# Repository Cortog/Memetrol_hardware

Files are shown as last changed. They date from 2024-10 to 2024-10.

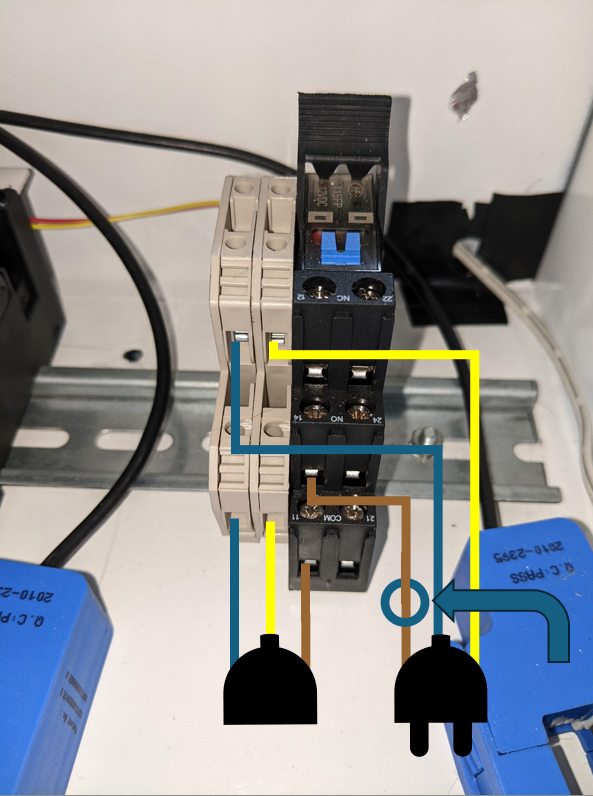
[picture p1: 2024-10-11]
relays_connection_diagram.png

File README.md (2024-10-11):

## Context
This repository contains the hardware design files for the Memetrol project. This project can control three washing machines and one dryer. Users can authenticate themselves using an RFID badge. The system logs the usage of the machines. A webserver on the system serves these logs to the administrator.

## Hardware
The hardware consists of a Raspberry Pi zero W and a Waveshare RP2040-zero both mounted on the base PCB. This PCB also contains the power supply, the relay drivers and analog circuitry for the current sensors. The Raspberry Pi is connected to the Waveshare RP2040-zero with UART. The Waveshare RP2040-zero is connected to the relay drivers and the current measurement circuitry. The Raspberry Pi is connected to the rest of the peripherals using a 20 pin ribbon cable. This cable goes to the door PCB, at which point the connections to the buttons, the LCD and the RFID reader are broken out.

## Changes for the next revision
- Not enough mounting holes were placed on the main PCB. In the end I drilled out the 2.5 mm mounting holes for the Raspberry Pi to 3 mm and drilled an extra one here: [image](extra_hole_location.png). In a future revision the mounting holes should be placed in the correct locations.
- R25 was not needed. This is the resistor in series with the buzzer. The volume can be controlled by varying the duty cycle of the PWM signal. This resistor should be removed in the next revision.
- The buzzer is not loud enough, a different buzzer should be used.
- The connectors for the relays should be changed, currently it consists of two connectors, one for + and one for ground. It should be changed to four connectors, one for each relay, this makes the connections more clear. The current labeling on the PCB is also not correct, where it says Ground it should be 12 volt.
- The analog circuitry for the current measurement could have its own 3.3 volt, or even a 1.65 volt regulator, this might make the measurements more stable.
- The rp2040-zero should know if the override switches are pressed, this would make calibration easier, since the rp2040-zero can then know if it should be measuring zero current or not.
- The electrolytic capacitors in the analog circuitry could be a lot smaller, these were only used because I had them laying around.
- An input power capacitory should be added.
- Maybe an aditional button should be added to the main PCB, this could be used for resetting passwords.
- In the current design a solderbridge is used to select between 5 volts and 12 volts for the button led power, with 12 volts being the default. However, the button leds can only handle up to 6 volts. The door PCB should be changed so that the leds can only be powered from the 5 volt rail.
- During the building of the PCB several mosfets broke, the gate was at around one volt even though it was being pulled down. After replacing them it was improved, but I also added a 10k resistor in parallel with the button leds which improved the leds realy turning off when the gate was being pulled down. This situation should be investigated further.
- Maybe an RFID interupt pin can be added to the door PCB, this would make the system more responsive and use less cpu time.
- The RFID and the LCD are on the same LCD bus, but this makes the RFID reader misbehave. Therefore it needs to be reset every time it is used. This should be fixed in the next revision.

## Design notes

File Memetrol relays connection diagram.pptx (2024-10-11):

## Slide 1

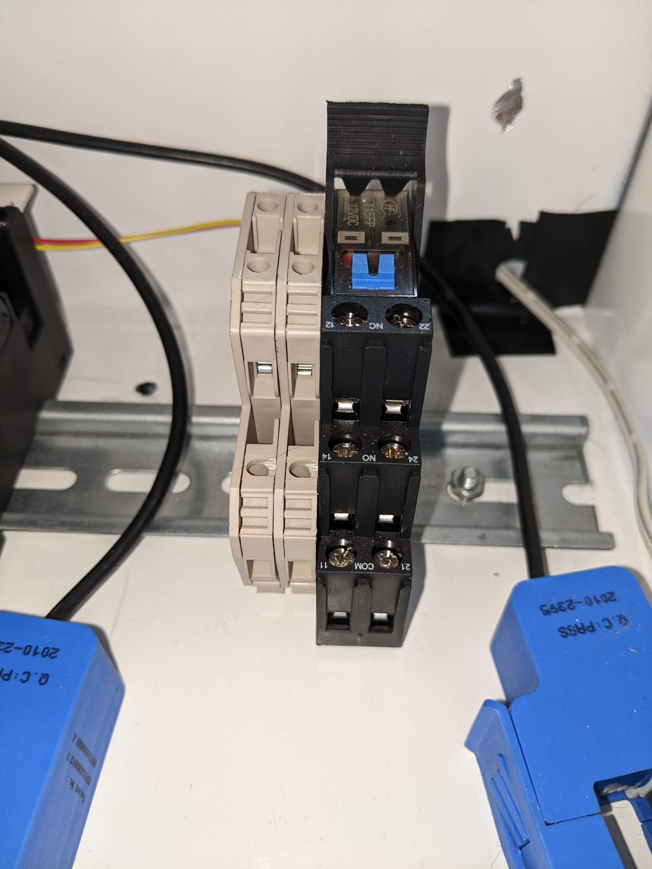
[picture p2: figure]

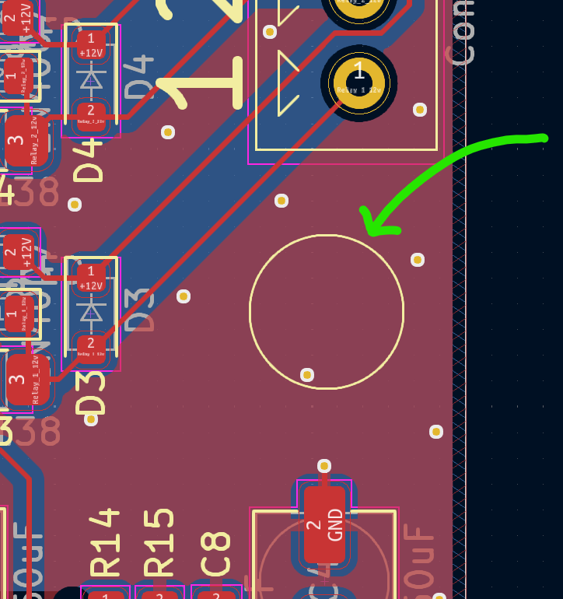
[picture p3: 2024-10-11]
extra_hole_location.png

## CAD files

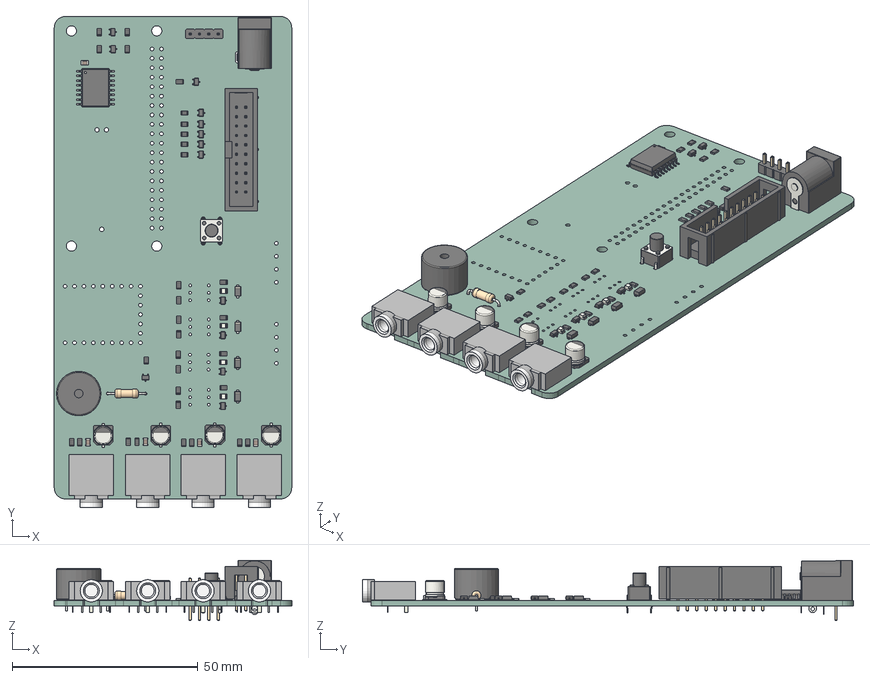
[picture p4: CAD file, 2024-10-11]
memetrol_base/memetrol_base.step
64.0 x 132.3 x 16.2 mm
R_0805_2012Metric x 31
C_0805_2012Metric x 5
SOIC_8_39x49mm_P127mm
LED_0805_2012Metric x 4
Jack_3.5mm_CUI_SJ1-3525N_Horizontal x 4
SOT_323_SC_70 x 13
CP_Elec_5x53 x 4
R_Axial_DIN0207_L63mm_D25mm_P1016mm_Horizontal
D_SOD_123F x 4
IDC_Header_2x10_P254mm_Vertical
SW_PUSH_6mm_h7.3mm
SOIC_16W_75x103mm_P127mm
BarrelJack_Horizontal
MagneticBuzzer_ProSignal_ABT_410_RC
PinHeader_1x04_P254mm_Vertical
memetrol_base_PCB

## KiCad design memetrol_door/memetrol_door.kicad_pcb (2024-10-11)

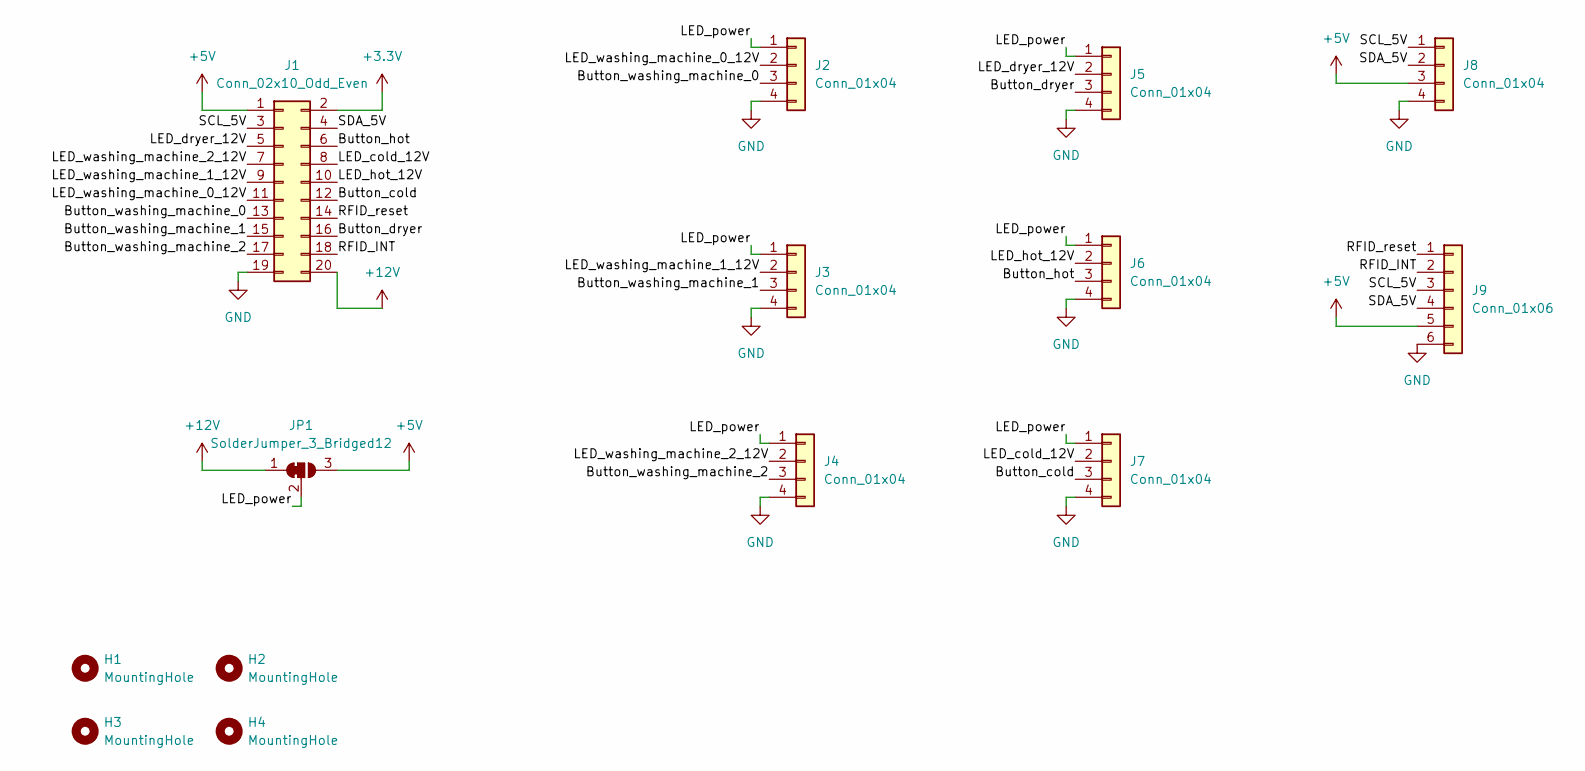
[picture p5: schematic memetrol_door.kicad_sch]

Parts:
H1, H2, H3, H4: MountingHole; MountingHole_3.2mm_M3
J1: Conn_02x10_Odd_Even; IDC-Header_2x10_P2.54mm_Vertical
J2, J3, J4, J5, J6, J7, J8: Conn_01x04; JST_PH_B4B-PH-K_1x04_P2.00mm_Vertical
J9: Conn_01x06; JST_PH_B6B-PH-K_1x06_P2.00mm_Vertical
JP1: SolderJumper_3_Bridged12; SolderJumper-3_P1.3mm_Bridged12_Pad1.0x1.5mm

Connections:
+3.3V: J1.2
+5V: J1.1, J8.3, J9.5, JP1.3 (B)
+12V: J1.20, JP1.1 (A)
/Button_cold: J1.12, J7.3
/Button_dryer: J1.16, J5.3
/Button_hot: J1.6, J6.3
/Button_washing_machine_0: J1.13, J2.3
/Button_washing_machine_1: J1.15, J3.3
/Button_washing_machine_2: J1.17, J4.3
/LED_cold_12V: J1.8, J7.2
/LED_dryer_12V: J1.5, J5.2
/LED_hot_12V: J1.10, J6.2
/LED_power: J2.1, J3.1, J4.1, J5.1, J6.1, J7.1, JP1.2 (C)
/LED_washing_machine_0_12V: J1.11, J2.2
/LED_washing_machine_1_12V: J1.9, J3.2
/LED_washing_machine_2_12V: J1.7, J4.2
/RFID_INT: J1.18, J9.2
/RFID_reset: J1.14, J9.1
/SCL_5V: J1.3, J8.1, J9.3
/SDA_5V: J1.4, J8.2, J9.4
GND: J1.19, J2.4, J3.4, J4.4, J5.4, J6.4, J7.4, J8.4, J9.6

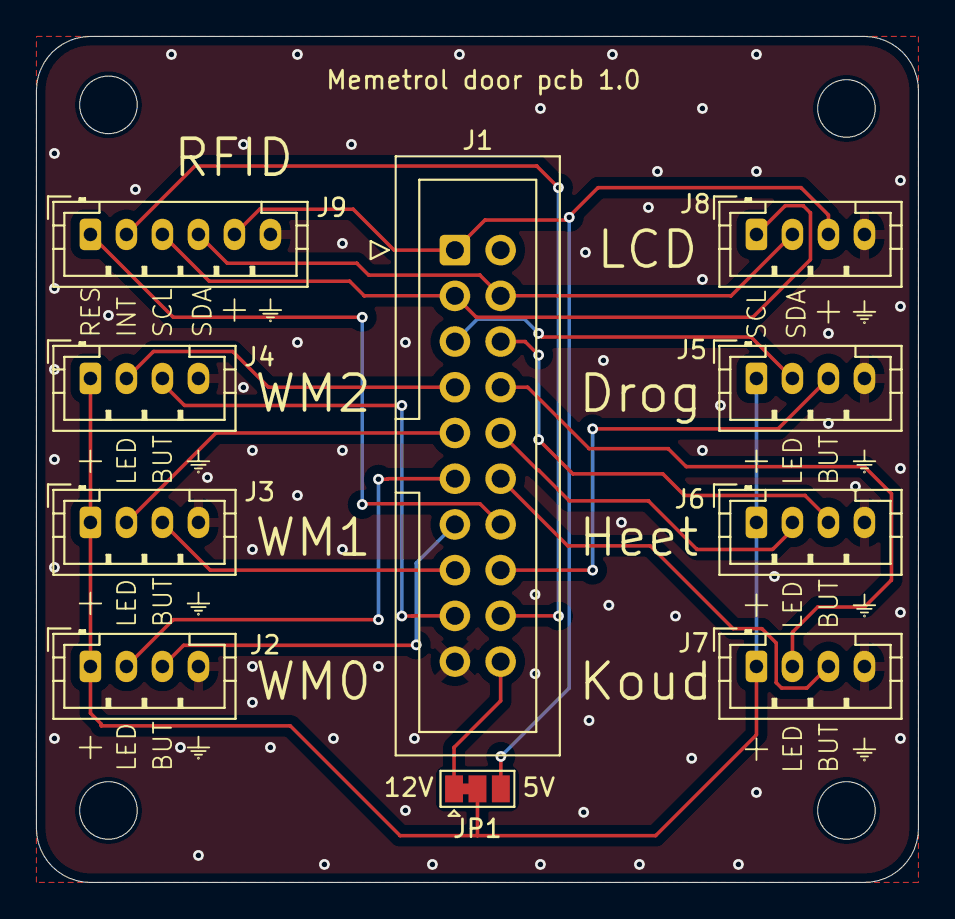
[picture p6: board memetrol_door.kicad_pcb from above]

Board: 2 copper layers, 49.0 x 47.0 mm, 14 parts (0 on the bottom side), 20 nets.

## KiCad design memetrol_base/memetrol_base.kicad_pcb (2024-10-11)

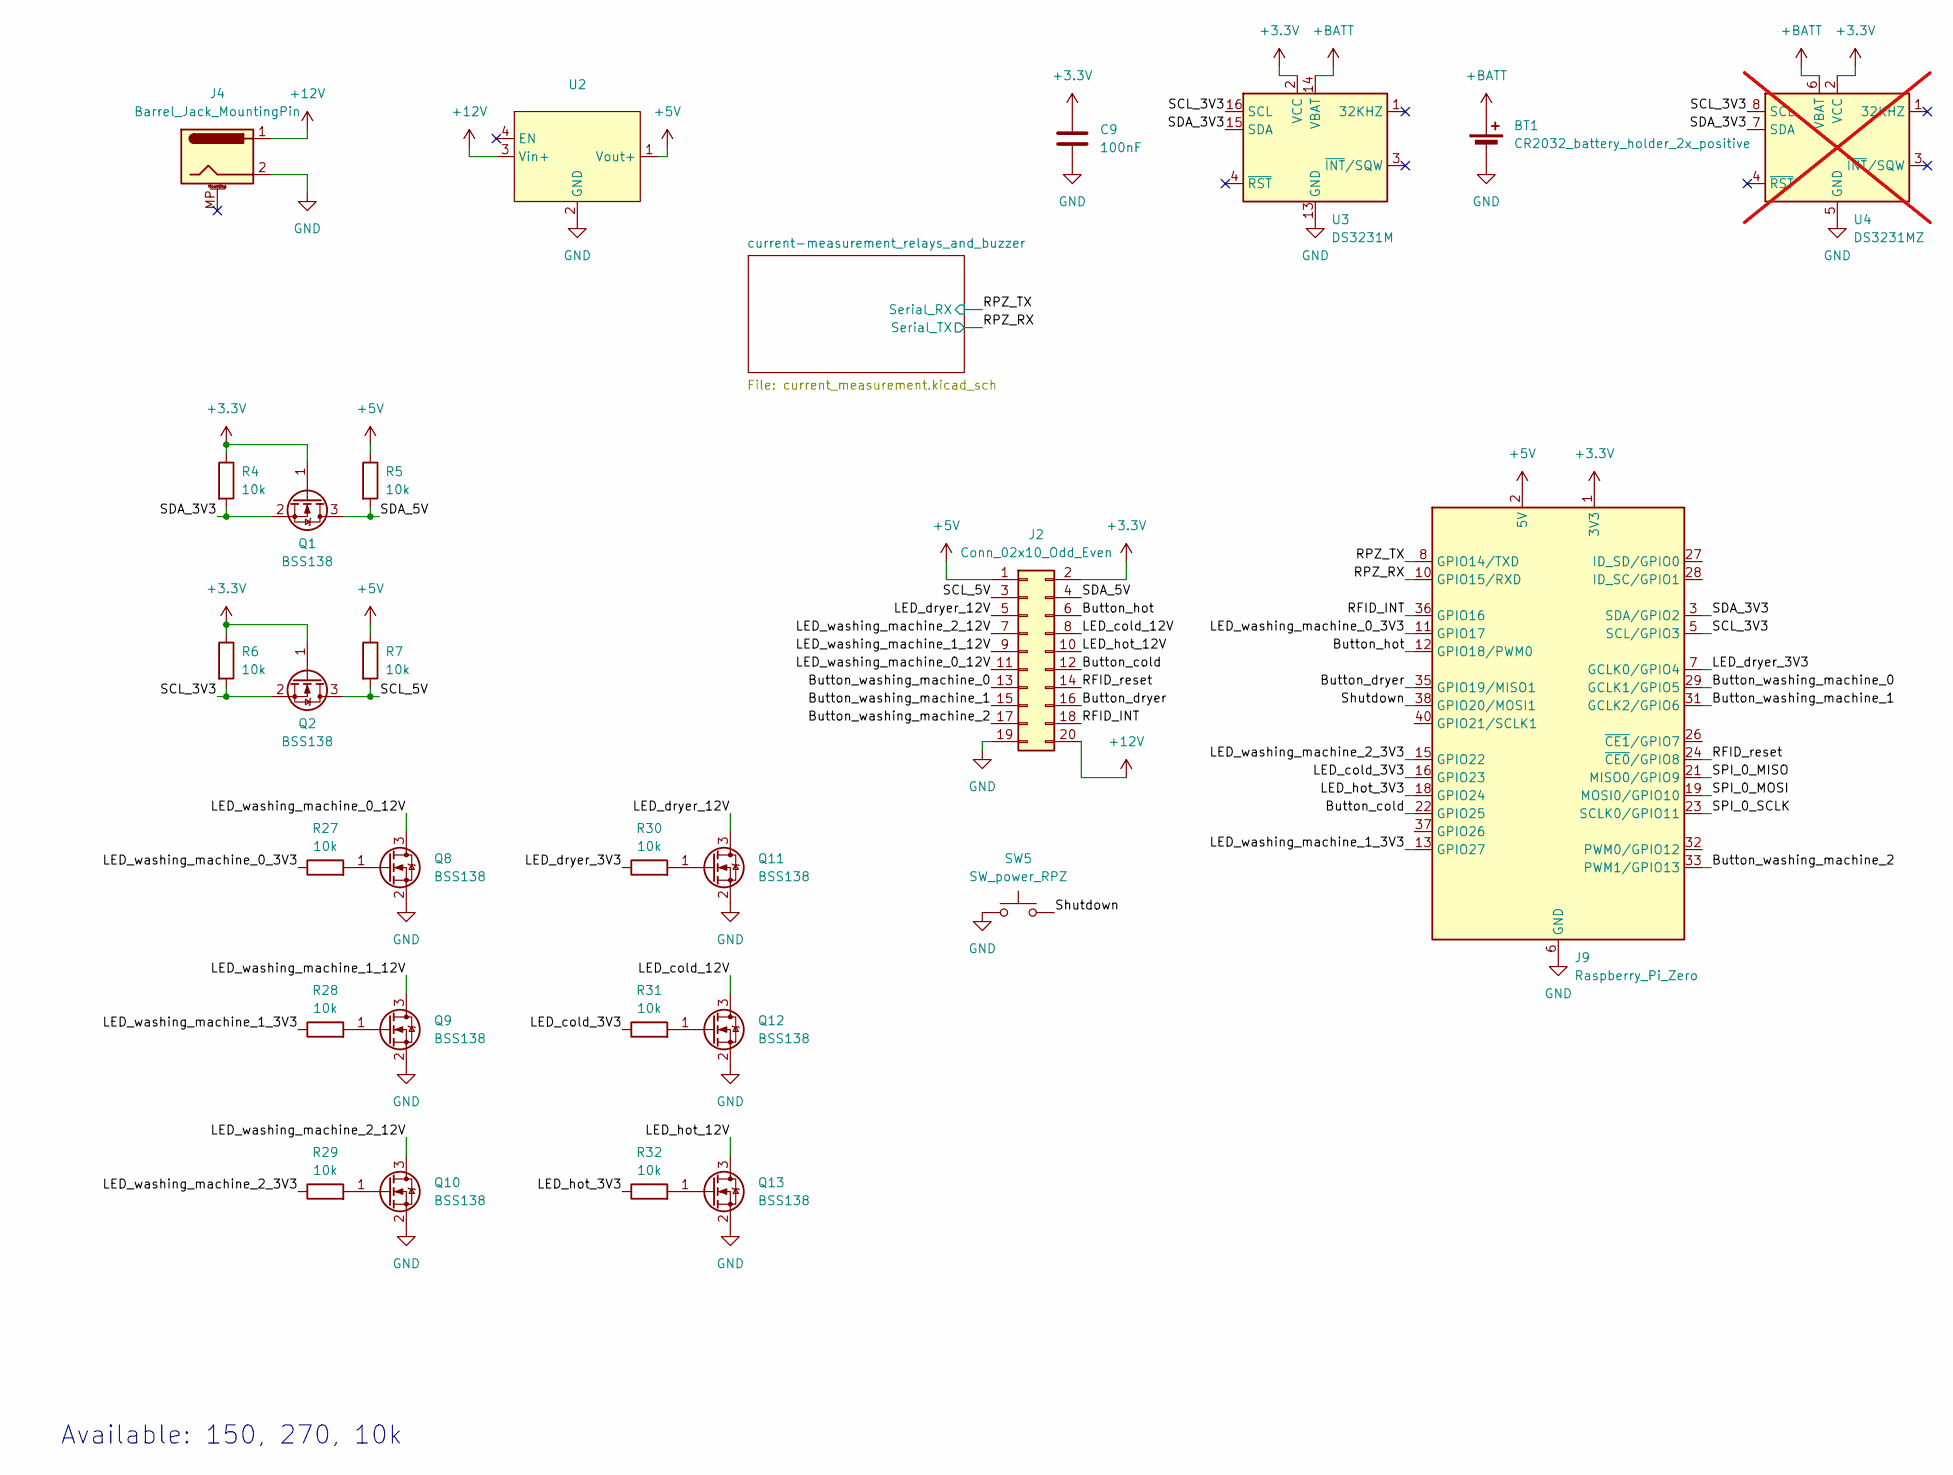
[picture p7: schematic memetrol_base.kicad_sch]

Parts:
BT1: CR2032_battery_holder_2x_positive; RS_PRO_CR2032_237-8358
C9: 100nF; C_0805_2012Metric_Pad1.18x1.45mm_HandSolder
J2: Conn_02x10_Odd_Even; IDC-Header_2x10_P2.54mm_Vertical
J4: Barrel_Jack_MountingPin; BarrelJack_Horizontal
J9: Raspberry_Pi_Zero; Raspberry_Pi_Zero_Socketed_THT_FaceUp_MountingHoles
Q1, Q2, Q8, Q9, Q10, Q11, Q12, Q13: BSS138; SOT-323_SC-70_Handsoldering
R4, R5, R6, R7, R27, R28, R29, R30, R31, R32: 10k; R_0805_2012Metric_Pad1.20x1.40mm_HandSolder
SW5: SW_power_RPZ; SW_PUSH_6mm_H7.3mm
U2: MP2315_board_vertical
U3: DS3231M; SOIC-16W_7.5x10.3mm_P1.27mm
U4: DS3231MZ; SOIC-8_3.9x4.9mm_P1.27mm; not fitted

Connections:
+3.3V: C9.1, J2.2, J9.1 (3V3), J9.17 (3V3), Q1.1 (G), Q2.1 (G), R4.1, R6.1, U3.2 (VCC), U4.2 (VCC)
+5V: J2.1, J9.2 (5V), J9.4 (5V), R5.1, R7.1, U2.1 (Vout+); also elsewhere on the board
+12V: J2.20, J4.1, U2.3 (Vin+); also elsewhere on the board
+BATT: BT1.1 (+), BT1.2 (+), U3.14 (VBAT), U4.6 (VBAT)
/Button_cold: J2.12, J9.22 (GPIO25)
/Button_dryer: J2.16, J9.35 (GPIO19/MISO1)
/Button_hot: J2.6, J9.12 (GPIO18/PWM0)
/Button_washing_machine_0: J2.13, J9.29 (GCLK1/GPIO5)
/Button_washing_machine_1: J2.15, J9.31 (GCLK2/GPIO6)
/Button_washing_machine_2: J2.17, J9.33 (PWM1/GPIO13)
/LED_cold_3V3: J9.16 (GPIO23), R31.1
/LED_cold_12V: J2.8, Q12.3 (D)
/LED_dryer_3V3: J9.7 (GCLK0/GPIO4), R30.1
/LED_dryer_12V: J2.5, Q11.3 (D)
/LED_hot_3V3: J9.18 (GPIO24), R32.1
/LED_hot_12V: J2.10, Q13.3 (D)
/LED_washing_machine_0_3V3: J9.11 (GPIO17), R27.1
/LED_washing_machine_0_12V: J2.11, Q8.3 (D)
/LED_washing_machine_1_3V3: J9.13 (GPIO27), R28.1
/LED_washing_machine_1_12V: J2.9, Q9.3 (D)
/LED_washing_machine_2_3V3: J9.15 (GPIO22), R29.1
/LED_washing_machine_2_12V: J2.7, Q10.3 (D)
/RFID_INT: J2.18, J9.36 (GPIO16)
/RFID_reset: J2.14, J9.24 (~CE0/GPIO8)
/RPZ_RX: J9.10 (GPIO15/RXD); also elsewhere on the board
/RPZ_TX: J9.8 (GPIO14/TXD); also elsewhere on the board
/SCL_3V3: J9.5 (SCL/GPIO3), Q2.2 (S), R6.2, U3.16 (SCL), U4.8 (SCL)
/SCL_5V: J2.3, Q2.3 (D), R7.2
/SDA_3V3: J9.3 (SDA/GPIO2), Q1.2 (S), R4.2, U3.15 (SDA), U4.7 (SDA)
/SDA_5V: J2.4, Q1.3 (D), R5.2
/SPI_0_MISO: J9.21 (MISO0/GPIO9)
/SPI_0_MOSI: J9.19 (MOSI0/GPIO10)
/SPI_0_SCLK: J9.23 (SCLK0/GPIO11)
/Shutdown: J9.38 (GPIO20/MOSI1), SW5.2
GND: BT1.3 (-), C9.2, J2.19, J4.2, J9.6 (GND), J9.9 (GND), J9.14 (GND), J9.20 (GND), J9.25 (GND), J9.30 (GND), J9.34 (GND), J9.39 (GND), Q8.2 (S), Q9.2 (S), Q10.2 (S), Q11.2 (S), Q12.2 (S), Q13.2 (S), SW5.1, U2.2 (GND), U3.5 (GND), U3.6 (GND), U3.7 (GND), U3.8 (GND), U3.9 (GND), U3.10 (GND), U3.11 (GND), U3.12 (GND), U3.13 (GND), U4.5 (GND); also elsewhere on the board
unnamed: Q8.1 (G), R27.2
unnamed: Q9.1 (G), R28.2
unnamed: Q10.1 (G), R29.2
unnamed: Q11.1 (G), R30.2
unnamed: Q12.1 (G), R31.2
unnamed: Q13.1 (G), R32.2

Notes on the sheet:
Available: 150, 270, 10k

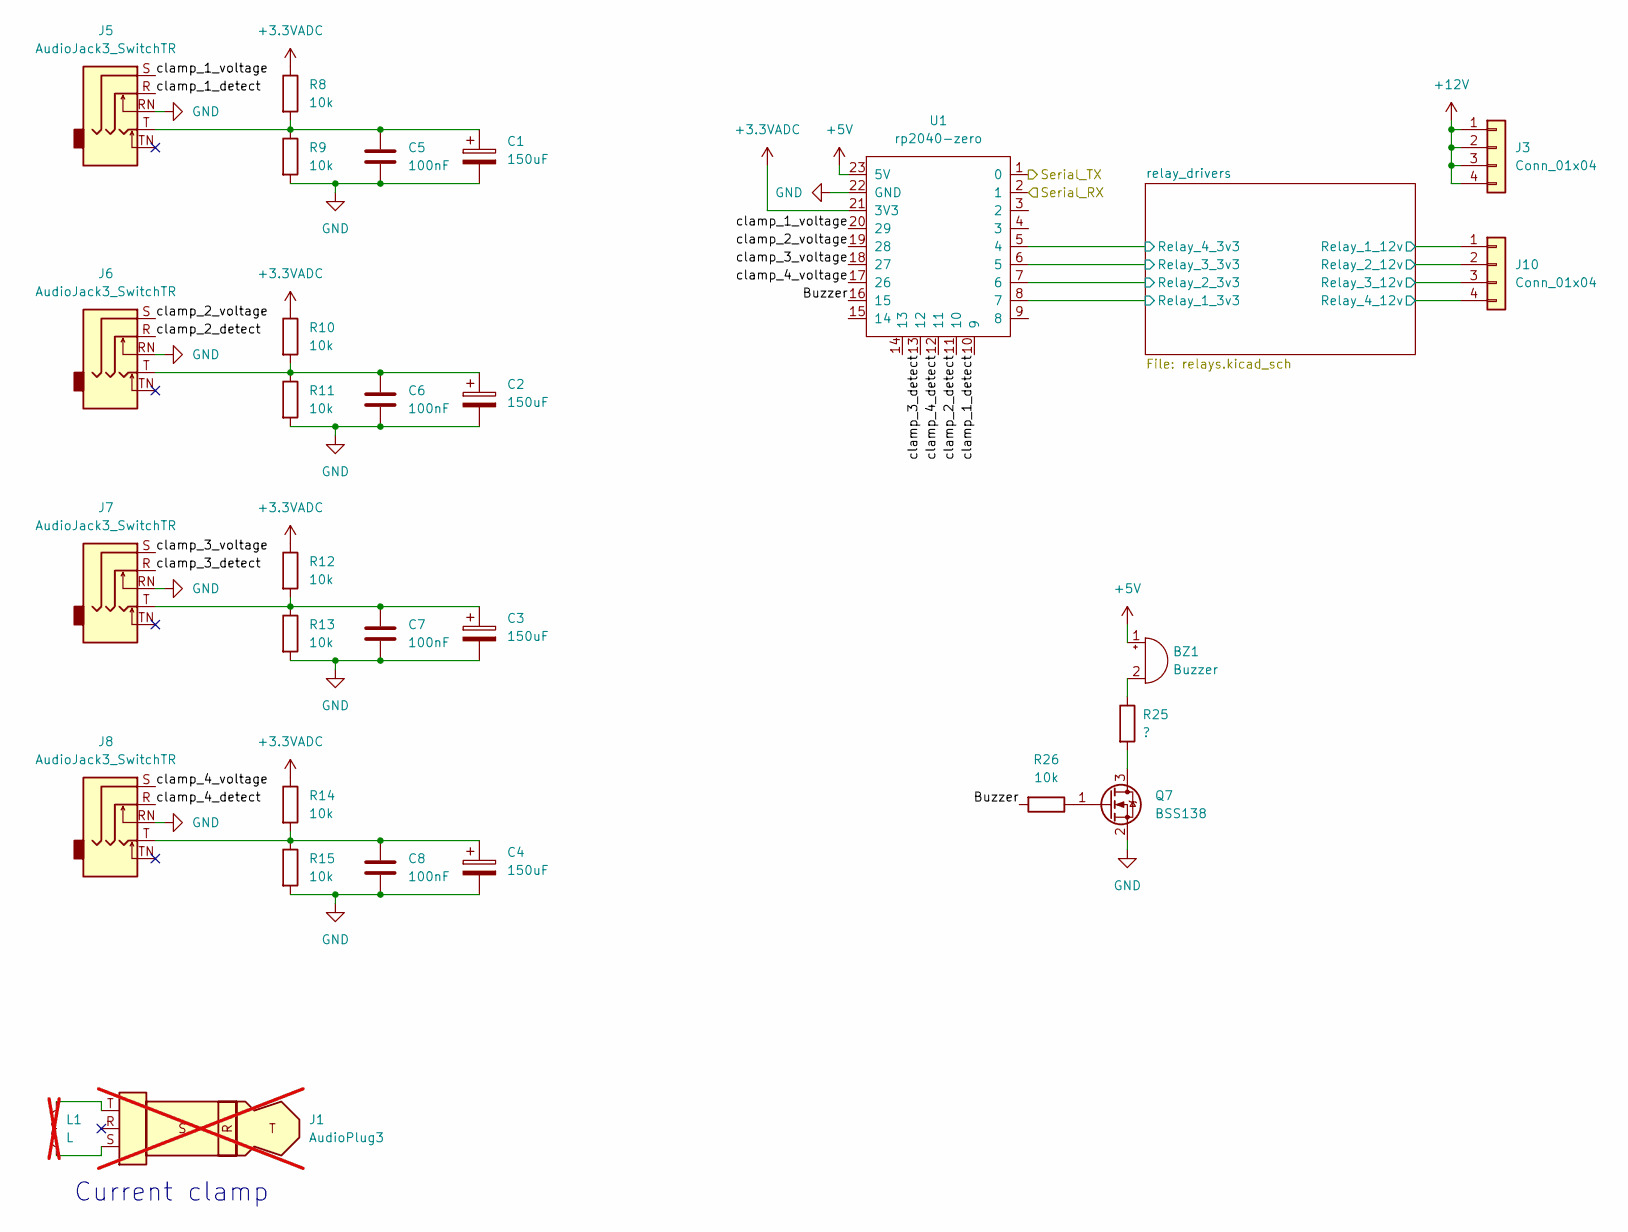
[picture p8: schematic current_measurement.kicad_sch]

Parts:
BZ1: Buzzer; MagneticBuzzer_ProSignal_ABT-410-RC
C1, C2, C3, C4: 150uF; CP_Elec_5x5.3
C5, C6, C7, C8: 100nF; C_0805_2012Metric_Pad1.18x1.45mm_HandSolder
J1: AudioPlug3; not fitted
J3, J10: Conn_01x04; 8971039
J5, J6, J7, J8: AudioJack3_SwitchTR; Jack_3.5mm_CUI_SJ1-3525N_Horizontal
L1: L; not fitted
Q7: BSS138; SOT-323_SC-70_Handsoldering
R8, R9, R10, R11, R12, R13, R14, R15, R26: 10k; R_0805_2012Metric_Pad1.20x1.40mm_HandSolder
R25: ?; R_Axial_DIN0207_L6.3mm_D2.5mm_P10.16mm_Horizontal
U1: rp2040-zero; rp2040-zero-tht

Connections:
+3.3VADC: R8.1, R10.1, R12.1, R14.1, U1.21 (3V3); also elsewhere on the board
+5V: BZ1.1 (+), U1.23 (5V); also elsewhere on the board
+12V: J3.1, J3.2, J3.3, J3.4; also elsewhere on the board
/RPZ_RX: U1.1 (0); also elsewhere on the board
/RPZ_TX: U1.2 (1); also elsewhere on the board
/current-measurement_relays_and_buzzer/Buzzer: R26.2, U1.16 (15)
/current-measurement_relays_and_buzzer/clamp_1_detect: J5.R, U1.10 (9)
/current-measurement_relays_and_buzzer/clamp_1_voltage: J5.S, U1.20 (29)
/current-measurement_relays_and_buzzer/clamp_2_detect: J6.R, U1.11 (10)
/current-measurement_relays_and_buzzer/clamp_2_voltage: J6.S, U1.19 (28)
/current-measurement_relays_and_buzzer/clamp_3_detect: J7.R, U1.13 (12)
/current-measurement_relays_and_buzzer/clamp_3_voltage: J7.S, U1.18 (27)
/current-measurement_relays_and_buzzer/clamp_4_detect: J8.R, U1.12 (11)
/current-measurement_relays_and_buzzer/clamp_4_voltage: J8.S, U1.17 (26)
/current-measurement_relays_and_buzzer/relay_drivers/Relay_1_3v3: U1.8 (7); also elsewhere on the board
/current-measurement_relays_and_buzzer/relay_drivers/Relay_1_12v: J10.1; also elsewhere on the board
/current-measurement_relays_and_buzzer/relay_drivers/Relay_2_3v3: U1.7 (6); also elsewhere on the board
/current-measurement_relays_and_buzzer/relay_drivers/Relay_2_12v: J10.2; also elsewhere on the board
/current-measurement_relays_and_buzzer/relay_drivers/Relay_3_3v3: U1.6 (5); also elsewhere on the board
/current-measurement_relays_and_buzzer/relay_drivers/Relay_3_12v: J10.3; also elsewhere on the board
/current-measurement_relays_and_buzzer/relay_drivers/Relay_4_3v3: U1.5 (4); also elsewhere on the board
/current-measurement_relays_and_buzzer/relay_drivers/Relay_4_12v: J10.4; also elsewhere on the board
GND: C1.2, C2.2, C3.2, C4.2, C5.2, C6.2, C7.2, C8.2, J5.RN, J6.RN, J7.RN, J8.RN, Q7.2 (S), R9.2, R11.2, R13.2, R15.2, U1.22 (GND); also elsewhere on the board
unnamed: BZ1.2 (-), R25.1
unnamed: C1.1, C5.1, J5.T, R8.2, R9.1
unnamed: C2.1, C6.1, J6.T, R10.2, R11.1
unnamed: C3.1, C7.1, J7.T, R12.2, R13.1
unnamed: C4.1, C8.1, J8.T, R14.2, R15.1
unnamed: J1.S, L1.1
unnamed: J1.T, L1.2
unnamed: Q7.3 (D), R25.2
unnamed: Q7.1 (G), R26.1

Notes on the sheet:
Current clamp

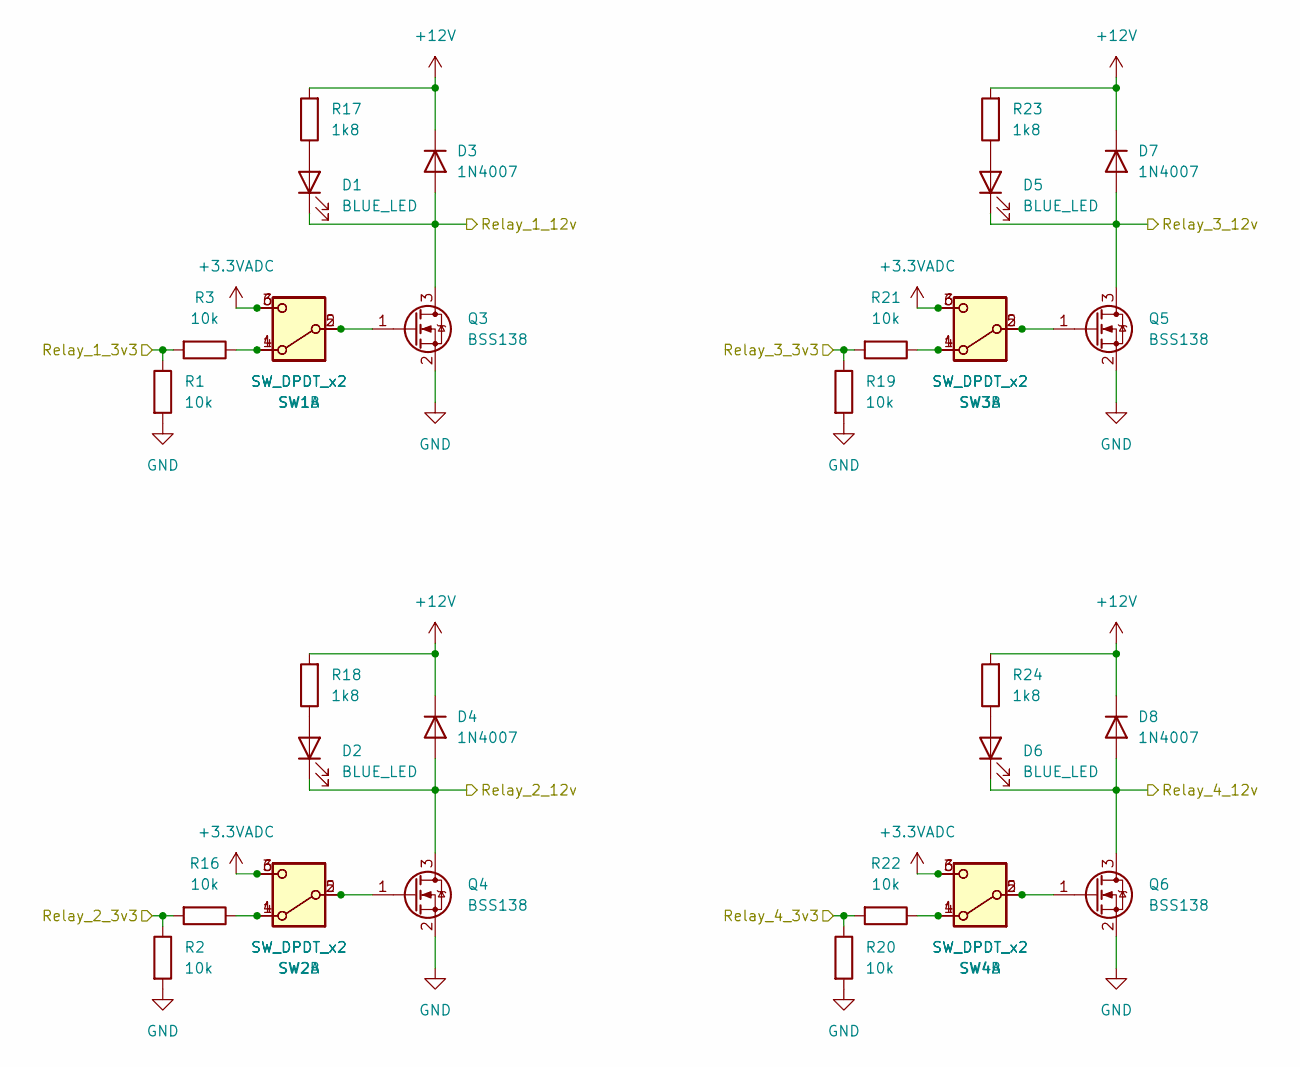
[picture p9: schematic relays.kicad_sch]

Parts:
D1, D2, D5, D6: BLUE_LED; LED_0805_2012Metric_Pad1.15x1.40mm_HandSolder
D3, D4, D7, D8: 1N4007; D_SOD-123F
Q3, Q4, Q5, Q6: BSS138; SOT-323_SC-70_large_drain
R1, R2, R3, R16, R19, R20, R21, R22: 10k; R_0805_2012Metric_Pad1.20x1.40mm_HandSolder
R17, R18, R23, R24: 1k8; R_0805_2012Metric_Pad1.20x1.40mm_HandSolder
SW1, SW2, SW3, SW4: SW_DPDT_x2; DPDT_7x7mm_blue-white

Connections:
+3.3VADC: SW1.3 (C), SW1.6 (C), SW2.3 (C), SW2.6 (C), SW3.3 (C), SW3.6 (C), SW4.3 (C), SW4.6 (C); also elsewhere on the board
+12V: D3.1 (K), D4.1 (K), D7.1 (K), D8.1 (K), R17.2, R18.2, R23.2, R24.2; also elsewhere on the board
/current-measurement_relays_and_buzzer/relay_drivers/Relay_1_3v3: R1.1, R3.2; also elsewhere on the board
/current-measurement_relays_and_buzzer/relay_drivers/Relay_1_12v: D1.1 (K), D3.2 (A), Q3.3 (D); also elsewhere on the board
/current-measurement_relays_and_buzzer/relay_drivers/Relay_2_3v3: R2.1, R16.2; also elsewhere on the board
/current-measurement_relays_and_buzzer/relay_drivers/Relay_2_12v: D2.1 (K), D4.2 (A), Q4.3 (D); also elsewhere on the board
/current-measurement_relays_and_buzzer/relay_drivers/Relay_3_3v3: R19.1, R21.2; also elsewhere on the board
/current-measurement_relays_and_buzzer/relay_drivers/Relay_3_12v: D5.1 (K), D7.2 (A), Q5.3 (D); also elsewhere on the board
/current-measurement_relays_and_buzzer/relay_drivers/Relay_4_3v3: R20.1, R22.2; also elsewhere on the board
/current-measurement_relays_and_buzzer/relay_drivers/Relay_4_12v: D6.1 (K), D8.2 (A), Q6.3 (D); also elsewhere on the board
GND: Q3.2 (S), Q4.2 (S), Q5.2 (S), Q6.2 (S), R1.2, R2.2, R19.2, R20.2; also elsewhere on the board
unnamed: D1.2 (A), R17.1
unnamed: D2.2 (A), R18.1
unnamed: D5.2 (A), R23.1
unnamed: D6.2 (A), R24.1
unnamed: Q3.1 (G), SW1.2 (B), SW1.5 (B)
unnamed: Q4.1 (G), SW2.2 (B), SW2.5 (B)
unnamed: Q5.1 (G), SW3.2 (B), SW3.5 (B)
unnamed: Q6.1 (G), SW4.2 (B), SW4.5 (B)
unnamed: R3.1, SW1.1 (A), SW1.4 (A)
unnamed: R16.1, SW2.1 (A), SW2.4 (A)
unnamed: R21.1, SW3.1 (A), SW3.4 (A)
unnamed: R22.1, SW4.1 (A), SW4.4 (A)

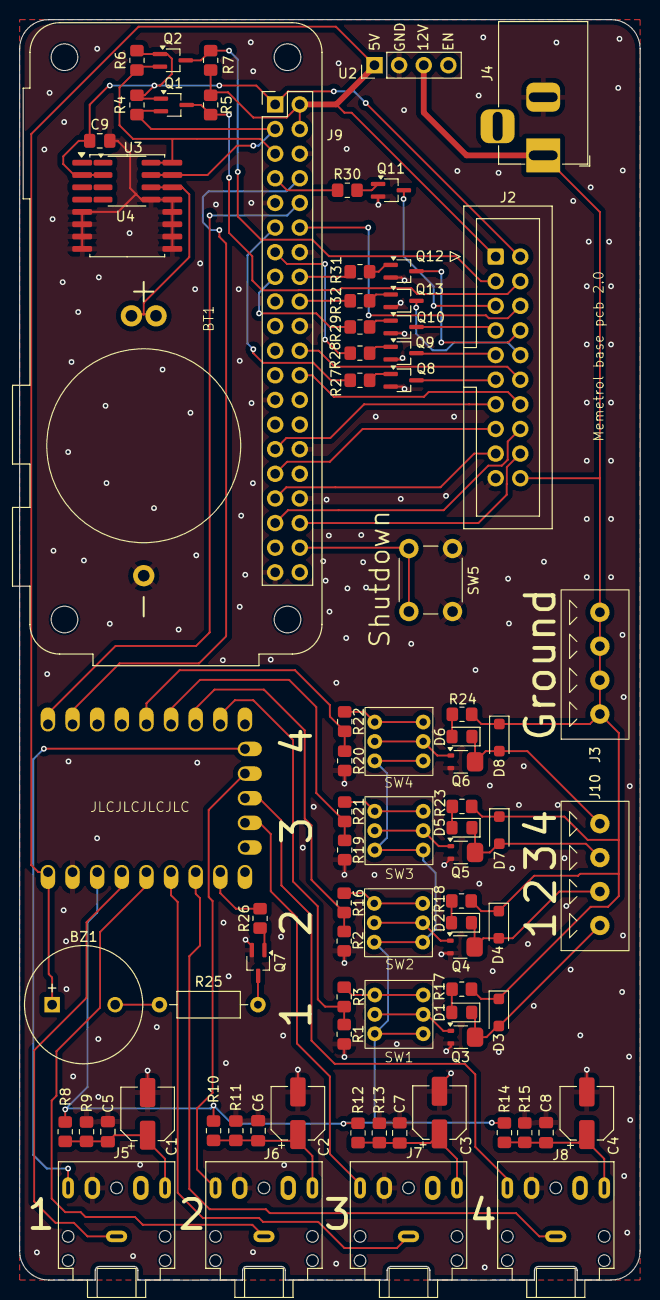
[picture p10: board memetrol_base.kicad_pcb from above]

Board: 2 copper layers, 64.0 x 130.0 mm, 82 parts (0 on the bottom side), 75 nets.
